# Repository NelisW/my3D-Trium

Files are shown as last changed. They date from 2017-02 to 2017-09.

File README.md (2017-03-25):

# Note

This repository is no longer actively maintained.

The contents of this repository is not an endorsement of the Trium printer. I keep it alive on request of some Trium owners.  

I stopped working on the Trium and I am considering buying another printer.

My own experiences with the Trium is rather negative. 
- If you want to buy a good delta frame to serve as a basis for your own delta printer, it is probably a reasonable design (although I am convinced you can get a less expensive delta frame).
- If you want to learn how to refurbish and rebuild delta printers, this is also a fair kit to buy.
- If you want a printer to print parts and not spend countless hours to get the printer going, rather go buy a well tested design with a large user base. The [Josef Prusa Original i3 MK2](http://shop.prusa3d.com/en/) (not some cheap rip-off) does not cost significantly more than the Trium is has a good reputation (but do your own research).

# Purpose

This repo serves to capture the experience of a number of Trium 3D printer builders.

This repo document is not official Trium information and does not endorse the product in any way. You will find that most Trium users are loyal to the product, but do your own research before committing to a purchase.

The reference information for Trium construction is the [E-Mergin Innovation](https://emergin.net/) Trium printer's  [User Manual (Ver 0.15)](https://emergin.net//user-manual/)  and the assortment of  [videos  on YouTube](https://www.youtube.com/watch?v=81HdwWcrpt0&list=PLMmAHPJoXlL8cp_-7R_6Hdb887jVPCUp3).

This repo contains information that is supplementary to the E-Mergin reference documentation and serves to capture some of the information
-  found on the [Trium ProBoard web site](http://trium3d.proboards.com),
-  found on the [Trium Facebook page](https://www.facebook.com/groups/emergin/) (For my own part, I find the Facebook interface confusing and I don't spend much time there), 
-  learned by a few builders when contructing their Trium printers, and 
-  found on the internet,

# Contents

- [Building the Trium printer](https://github.com/NelisW/my3D-Trium/blob/master/building/Trium-build.md)
- [Calibrating the Trium printer](https://github.com/NelisW/my3D-Trium/blob/master/building/Trium-calibration.md)
- [My views on the Trium printer](https://github.com/NelisW/my3D-Trium/blob/master/building/Trium-gripes.md)

# License

The information presented in this repo is distributed under the MIT license, please see the LICENSE file in this repo.

In particular, please note that 

THE SOFTWARE IS PROVIDED "AS IS", WITHOUT WARRANTY OF ANY KIND, EXPRESS OR
IMPLIED, INCLUDING BUT NOT LIMITED TO THE WARRANTIES OF MERCHANTABILITY,
FITNESS FOR A PARTICULAR PURPOSE AND NONINFRINGEMENT. IN NO EVENT SHALL THE
AUTHORS OR COPYRIGHT HOLDERS BE LIABLE FOR ANY CLAIM, DAMAGES OR OTHER
LIABILITY, WHETHER IN AN ACTION OF CONTRACT, TORT OR OTHERWISE, ARISING FROM,
OUT OF OR IN CONNECTION WITH THE SOFTWARE OR THE USE OR OTHER DEALINGS IN THE
SOFTWARE.

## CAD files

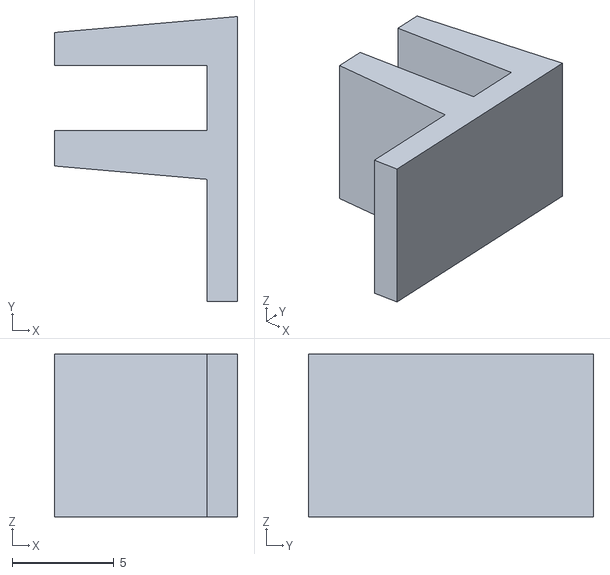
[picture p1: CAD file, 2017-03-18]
parts/TriumSliderHat.stl
9.00 x 14.0 x 8.00

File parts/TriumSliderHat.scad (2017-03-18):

// small part that fits over the slider top to provide
// a better seating area for the end-stop switch

length = 8; // total length
basewidth = 8.;
baseheight = 9.;
overhang = 6.;
overdepth = 1.5;
slotwidth = 3.2;
slotdepth = 8;

rotate([0,-90,0]){
difference(){
union(){
    difference(){
        translate([0,-basewidth/2.,0])
            cube([length,basewidth,baseheight]);
        translate([0,-slotwidth/2.,1.5])
            cube([length,slotwidth,slotdepth]);
    }
 
    translate([0,-overhang-basewidth/2.,0])
        cube([length,basewidth+overhang,overdepth]);
 }
        translate([0,basewidth/2.,0])
            rotate([5,0,0])
                cube([length,2,10]);
   translate([0,-basewidth/2,overdepth])
        rotate([-5,0,0])
            translate([0,-2,0])
                cube([length,2,10]);

}
}

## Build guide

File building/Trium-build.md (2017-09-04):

# Building the Trium Printer

The reference information for Trium construction is the E-Mergin Innovation [User Manual (Ver 0.15)](https://emergin.net//user-manual/)  and the assortment of  [videos  on YouTube](https://www.youtube.com/watch?v=81HdwWcrpt0&list=PLMmAHPJoXlL8cp_-7R_6Hdb887jVPCUp3).

This document is supplementary to the E-Mergin reference documentation and serves to capture some of the information
-  found on the [Trium ProBoard web site](http://trium3d.proboards.com),
-  found on the [Trium Facebook page](https://www.facebook.com/groups/emergin/) (For my own part, I find the Facebook interface confusing and I don't spend much time there), 
-  learned by a few builders when constructing their Trium printers, and 
-  found on the internet,

Several Trium users also freely share their findings and proposals for improvement. MiR did a good job of documenting the build process [here](http://trium3d.proboards.com/thread/67/notes-building-trium-standard-diamond).  This document borrows text and pictures freely from MiR's write up. Several others also contribute freely to the forum and the facebook page and also made comments to this document, these users include janlu, Rajaa Kahel, mikeeitel, Bill B, digid, and others.

References to page numbers in the Trium User Manual (Rev 0.15) are given as pNN.

I am not yet finished building my Trium, neither am I in too much of a hurry to do this quickly. The document will be updated every day or two with the latest information as I proceed. Visit here often to make sure you get the latest version.

This is my first printer and, despite my prior reading, the opened box posed quite a daunting picture. I enjoy writing and sharing  ([here](http://spie.org/Publications/Book/2021423) and [here](https://github.com/NelisW/ComputationalRadiometry)), so I decided to write up my experiences and learning  building up the printer. This document is offered in an effort to help others - especially novice 3d printer builders. My own status as a novice means that I can address some of your questions. I do not provide any guarantee, nor do I assume any liability for the content herein.  If it helps you I am happy, some other day perhaps you can help someone else. This is what open source is all about.

This write-up is somewhat overwhelming in detail and volume. Some proposals here are in the 'nice-to-have' category, e.g., EMI filter, optocoupler bed level sensor interface, etc. Read through the doc, review these proposals and  implement what makes sense to you.  Building the printer should be based on common sense and your intuition. It is however important to read a lot and read widely to ensure that you make an informed decision.  

**Note:** Most of the work we do on the Top Plate electronics and extruder is in the upside-down orientation, which means that left and right are switched.  I frequently found myself forgetting this - always think about the Top Plate assembly orientation when considering left/right or the tower naming convention.

**Note:** Test and review at every step along the build process. You want to catch issues early and not at the end, forcing you to disassemble the printer.  If something is not clear,  search for information: Google is your friend!

**Note:** Get to know the sounds your printer makes. Listen carefully and try to understand what you are hearing.  These noises are the printer's way of speaking to you: learn the langauge.

http://reprapandme.blogspot.co.za/2013/12/the-basics.html

# Tools and consumables

During the course of the build process you would purchase some parts or materials to complete some actions. Most of these are listed below in context of the building process. I recommend that you also consider purchasing the following in some cases you only need a pinch or small scrap! Most of these I would never use in the printer itself, but if you need an M2x25 in the middle of the night, you will be glad having these around.

- A set of machine screws, nuts and washers.  I bough 10 each of M2x6, M2x10, M2x16, M2x20, M2x25, M3x6, M3x10, M3x16, M3x20, M3x25,  M4x6, M4x10, M4x16, M4x20, M4x25, M5x6, M4x10. With as many nuts and washers. 
- A 2 cm strip of thin double sided  tape (not the kind you mount mirrors with).
- A 10 cm strip of magic sticky tape.
- A roll or two of non-adhesive teflon plumbing tape.
- Heat conducting paste (check the operating temperature range, you need at least 260 deg C).
- Cable ties (small) to bind cables into bundles.
- Heat shrink in a variety of sizes.
- Thin machine oil for the ball joints - use sparingly!
- Optional: a six way screw-down terminal block
- Optional: latex or nitrile (medical) gloves  when you work with sticky or lubrication products.
- Optional: in case you need this, some 14 SWG (or 2.5mm2) wire and 22 SWG hookup wire in black and red.
- Optional: some self-adhesive Kapton tape.
- Optional: Loctite thread lock or equivalent - but be careful, once stuck it is hard to remove a screw.

The following tools will come in handy:

- Essential: A set of Allen keys.
- Essential: A set of spanners or wrenches, down to 5 mm. A 7 mm spanner is required to fit the nozzle.
- Essential: A set of jeweller's screw drivers with Allen, Philips and flat heads.
- Essential: Two long nose pliers (short and long).
- Essential: Side cutter.
- Essential: Pencil-style craft knife.
- Essential: Set of flat and Philips screwdrivers.
- Small regular pliers.
- Tweezers.
- A magnifying glass, and/or a ([low magnification](https://www.amazon.co.uk/d/Magnifying-Glasses/Carson-LumiLoupe-Power-Stand-Magnifier/B000CAHCQS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)) 10X [loupe](https://en.wikipedia.org/wiki/Loupe)(jeweller's eyepiece)   to inspect the PCBs and other parts - and your subsequent print quality.
- A toothbrush to brush loosened away debris when cleaning solder bridges from  PCBs.
- Hand drill and drill bits - only used a few times.
- Optional but highly recommended!: a multimeter that can measure AC volts, DC volts, resistance, and possible temperature with a thermocouple.
- Optional: Cutting board or other work surface (don't work on your Oak or Rhodesian Teak dining table).
- Optional but really useful: Heat gun for shrink sleeving. Also used later to heat up the print bed or prints.
- Optional but really useful: Digital or manual vernier caliper. Also used later when calibrating the printer.
- Optional: a k-type thermocouple thermometer that can operate up to 300 deg C. Required to build trust in/calibrate the thermistor.
- Optional: Dremel, but this is just really to play with. I used it once in the TRIUM construction.
- Optional: a set of feeler gauges to use instead of the sheet of paper when setting up the nozzle-bed distance.

You may also find it necessary to have some parts printed using a printing service, simply because your own printer is not working yet.

# Conventions

## Towers
E-Mergin refers to the three vertical parts as "beams".  Beams, in construction, refer to a part that experiences lateral forces. Such parts are normally horizontal and carry downward forces such as weight.  In this document I prefer to use the word "tower" or "column", which signifies a vertical structure.

Label cables for future reference.

There could be confusion with delta printers because the towers are designated by X, Y, and Z, and the cartesian printer coordinates are also designated by the same three letters.  For the purposes of this document the towers are defined in capital letters X,Y, and Z, whereas the coordinate system axes are designated by lower case letters x, y, and z.

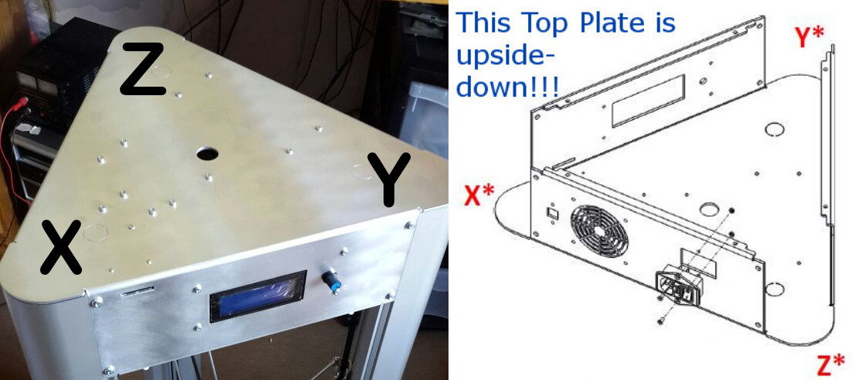
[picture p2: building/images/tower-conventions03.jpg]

[Looking at the front of the printer](https://groups.google.com/forum/#!msg/deltabot/nGpbRPdhAz0/kueyazbXeXAJ) with the LCD facing you (p16):
- X tower is on the front left, Y tower is on the front right, and Z tower is in the middle back.
- The origin (x,y)=(0,0) is in the center between the towers.  This is different from a Cartesian printer where the origin is in some corner.
- Increasing x is left to right, movement to the left of center is -x, and movement to the right is +x
- Increasing y is front to back (toward Z tower). Movement towards the front is -y, movement toward the back is +y.
- z movement is up and down. Touching the print surface is z=0, z_zero or z_min.
- All axis home in the MAX direction
- In the firmware `configuration.h` file the x,y Min/Max values are defined as
		#define DELTA_PRINTABLE_RADIUS 110.0
		#define X_MAX_POS DELTA_PRINTABLE_RADIUS
		#define X_MIN_POS -(DELTA_PRINTABLE_RADIUS)
		#define Y_MAX_POS DELTA_PRINTABLE_RADIUS
		#define Y_MIN_POS -(DELTA_PRINTABLE_RADIUS)
- issue G1 X-50 Y0, Z0: then X will move up, Y will move down and Z will not move. You can also manually move the end effector with the power off and verify it.

## (x,y,z) coordinate system
The following picture obtained [here](https://print3d.com.pk/wp-content/uploads/2015/09/Delta-Kossi-Build-Manual.pdf) shows the coordinate system (not the tower naming) convention in graphical form:
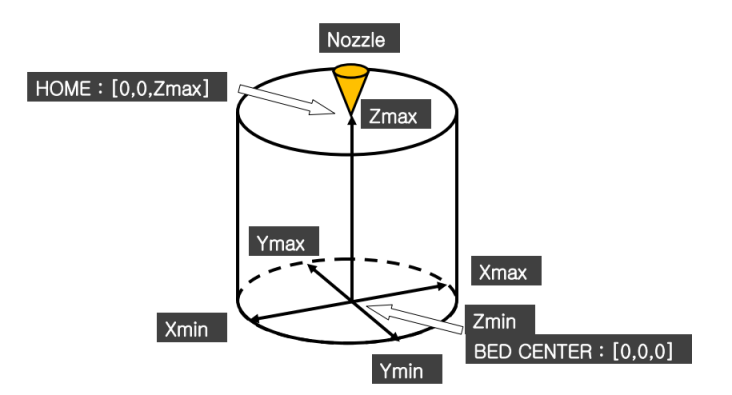
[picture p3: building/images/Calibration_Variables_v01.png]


## Reuleaux print area

A delta printer's print area is defined by the reach of all three delta arms and the actual print area is a clipped [Reuleaux triangle](https://en.wikipedia.org/wiki/Reuleaux_triangle) according to [Ryan Carlyle](https://groups.google.com/forum/#!topic/deltabot/xH_FIgClU9k).    The actual Trium print area will be the intersection of the hot bed circle and the Trium's Reuleaux triangle.

# Notes

## Software

This document does not cover software issues.  Before using the printer be careful to [set up the software](https://www.youtube.com/watch?v=bPBlYPV2sME&index=19&list=PLMmAHPJoXlL8cp_-7R_6Hdb887jVPCUp3) to the correct settings. In particular, the slicers must be set up for the Trium delta printer defaults.  The slicer software does *not* work correctly by default straight from the box.

## Noise damping

The all-metal Trium frame is superbly stiff and stable.  However the stiffness means that it resonates well (and at high frequency) and hence propagates vibration noise very, very well. This increases the overall noise level: anything that moves anywhere causes some resonance noise somewhere else.  For this reason apply vibration damping where ever you can. A case in point: slide a metal object across the Top Plate air vents; they ring very nicely at a high frequency. Fixing some rubber or silicon to the inside of the vent strips should reduce this particular vibration mode.  Fortunately, because of the superb frame stiffness the resonance frequencies are quite high - which means small displacements with lower energy; which should be easier to dampen.
- There is  a [design for a set of damping foot pads](https://www.facebook.com/groups/emergin/permalink/1870842983153461/) on [thingiverse](http://www.thingiverse.com/thing:2041200).
- You can use noise dampers on the tower stepper motors (see below).
- Rajaa replaced the rod-retaining springs with a rubber band to reduce spring noise.
- Replacing the DRV8825 drivers with [TMC2100 drivers]( https://www.facebook.com/groups/emergin/permalink/1869317553306004/) (not yet fully sorted out).
- Add an inline switch to the print cooling fans so that they can be switched off when not used. Do *not* switch off the fans on the electronics or print head heat sink.
- Jean Marc Cierniewski investigated using [small o-rings when mounting fan ducts](https://www.facebook.com/groups/emergin/permalink/1871767846394308/), but believes that there is more vibration on the rods.  However, using these o-rings on the main cooling fan mounted to the aluminium frame made a big difference.  You could also use rubber grommets to mount the fan.
- I pushed in a narrow strip of high density packing foam between the power supply and the Top Plate air vents to dampen the vibration of the vent strips.  There is a little vibration, but it diminishes quickly.
- I also put compacted  plastic foam sheeting inside each tower to dampen the ringing.

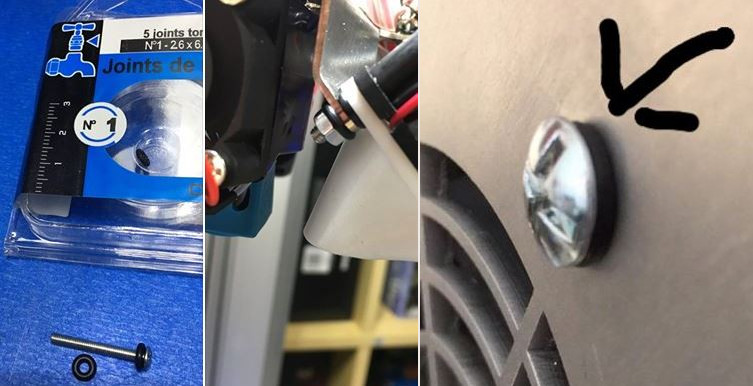
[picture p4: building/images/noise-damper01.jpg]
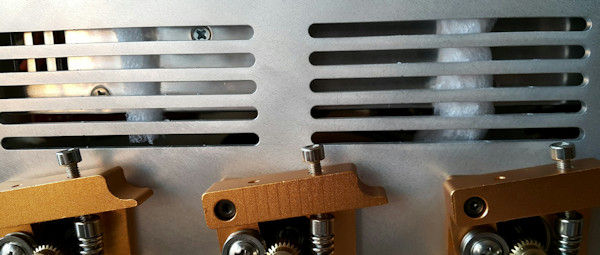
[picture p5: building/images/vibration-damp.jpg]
 

## Electrical supply safety

If wired correctly, the electricity supply convention in most parts of the world (except the US, it seems) is as follows:

- The green (or green/yellow) wire is 'ground'/'earth',  linked to a low resistance peg driven into the soil at your house, fixed to a conducting water pipe or linked to a peg driven into the soil at your electricity utility connection point (in the street or at a local substation).  This is the best reference of zero voltage under normal conditions.   If your feet are touching wet soil and you touch the earth/ground wire nothing will happen.
- The blue wire is 'neutral' (also known as null) meaning that it should normally be at a low voltage relative to earth. Depending on the local electricity safety code, neutral is normally connected to earth/ground at the point where the electricity enters your house. If your feet are touching wet soil and you touch the neutral wire nothing will happen under normal circumstances.
- The brown wire is 'live' and is at 115 or 230 V relative to neutral. This is the dangerous wire. Under normal circumstances the electricity flows between live and neutral. No current from live/brown ever flows to the green/earth wire (if it does, this is called a fault condition). If your feet are touching wet soil and you touch the live (brown) wire the electricity will flow from live, through your body and feet into the earth/ground, potentially killing you in a most unpleasant manner.
- Most electricity safety codes require a device (residual current device or earth leakage relay) which measures the difference in current flow between live and neutral. If this current exceeds some small value (20 mA) it means that some current from live is flowing to earth: an undesired fault condition.  The device then breaks the electricity supply - not because of over-current but because of current earth leakage.

All of the above apply when a three-pin connection is made to the electricity supply. If your country only have a two-pin supply or if your cable only has two pins and no earth conductor, the situation is very different. The wall plug can be plugged in in any orientation: there is no distinction between Live and Neutral any more. And even worse, there is no Earth connection.  Also, despite electricity safety codes' requirements, it may be that in some cases the Live and Neutral wires are exchanged, so that the terminal labelled with 'Neutral' may in fact be live.  This can happen is someone wired a plug the wrong way around - which happens frequently.  

According to [this video](https://www.youtube.com/watch?v=Bqar4cuVF_A), the colour code (or is it color code?) in the US is as follows. So please translate the colours to your local custom.  Please take the time and watch this video.

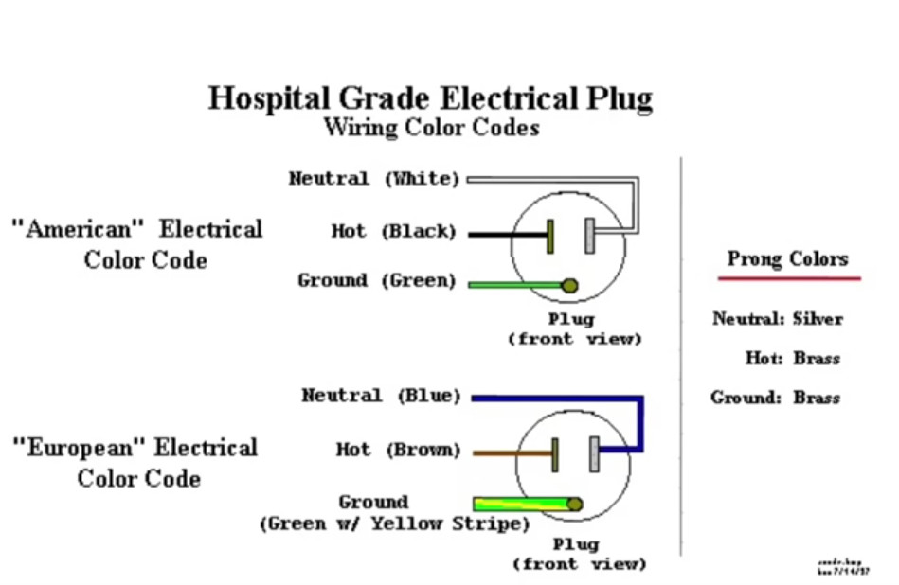
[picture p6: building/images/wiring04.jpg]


**So please consider the Neutral/Null and Live wiring in your printer as equally dangerous. Always afford Neutral the same respect you would show Live!**

**Never connect Neutral/Null or Live to Earth in the printer, it may lead to earth leakage conditions.**  Connecting Earth to Neutral is your electricity supply utility company's concern, they will do it according to their codes. Don't violate their codes by doing it yourself in your house or in your printer.

**Never connect Neutral/Null or Live to your Trium case,  or if your supply only has two wires, don't connect either to the case.**

### Connecting the Trium frame/case
At this point the issue of case earthing or grounding should be considered. The question is which of these do you connect and why?  There are three 'zero' potential locations to consider:

- Your 115/230V earth/ground, the green (green/yellow) wire from the house network (if Earth is available).
-  The Trium metal case.
-  The power supply zero voltage terminal (by convention zero voltage is normally the negative (black or -) terminal in the bipolar power supply, whereas the positive (red or +) is at some non-zero voltage (12V in this case).

The User Manual does not prescribe any connection: all three a disconnected from each other (if there are no connections inside the power supply, which is normally the case).  All three therefore 'float' with respect to each other: there can be some voltage between any of these.

If you are at all unsure, follow the Trium instruction, but just be very careful with the mains wiring!

For more information see [here](http://www.ese.upenn.edu/detkin/instruments/misctutorials/Ground/grd.html), [here](https://celectronics.com/pdf/IEEE11-9-05.pdf), and [here](http://www.allaboutcircuits.com/textbook/direct-current/chpt-3/safe-circuit-design/). See also [this video](https://www.youtube.com/watch?v=Bqar4cuVF_A)

#### Earth connection
If you have a three-pin electricity supply: 
Let us review connecting the electricity supply Earth to the Trium case with a secure and low resistance bond.  In this case the earth leakage protection will work if you accidentally touch the case and live.  The procedure is normally followed in domestic devices containing metal frames (bed lamps, clothing irons, stoves, kettles, etc.).  From a human safety and fire hazard perspective this is the safest approach.  You make your own decision.

If you have a two-pin electricity supply, there is no Earth to connect to the case. **Don't connect either of the two wires to the case**.

#### Power supply connection

It the printer electronics PSU module zero (black wire) is not connected to the frame, it means that the electronics reference floats with respect to the frame.  Any part of the electronics can touch the frame with no ill effect.  The disadvantage of this approach is the EMI is harder to control because the frame/case is floating with respect to the electronics.

If the power supply 0V negative/black is securely connected to the chassis, the case is not floating with respect of the electronics and EMI is easier to contain. However, because the frame is now at the 0V reference, if the +12V or some electronics output now touch the frame it will result in a short circuit fault, possibly destroying electronics components. For this reason some people prefer to fit a low resistance 100-1000 Ohm between the case and negative/black which will somewhat limit the current flow under fault conditions, but prevent electrostatic voltage build-up damage to the electronics.

#### Where to connect to the frame/case

Generally speaking, bonding the Earth (if done) and the printer power module to the case should be done at one point and one point only. Do not rely on the case to provide ground current flow (this will lead to earth loops and the EMi will be worse). So the electronics ground wiring should never touch the frame, except at this one point. In some cases it may have benefits to have the frame as ground plane, but it requires very careful design and is outside the scope of this project.

My preference would be to take two wires (one from green/earth and one from negative black) and connect both to a single point on the chassis.  You decide for yourself.

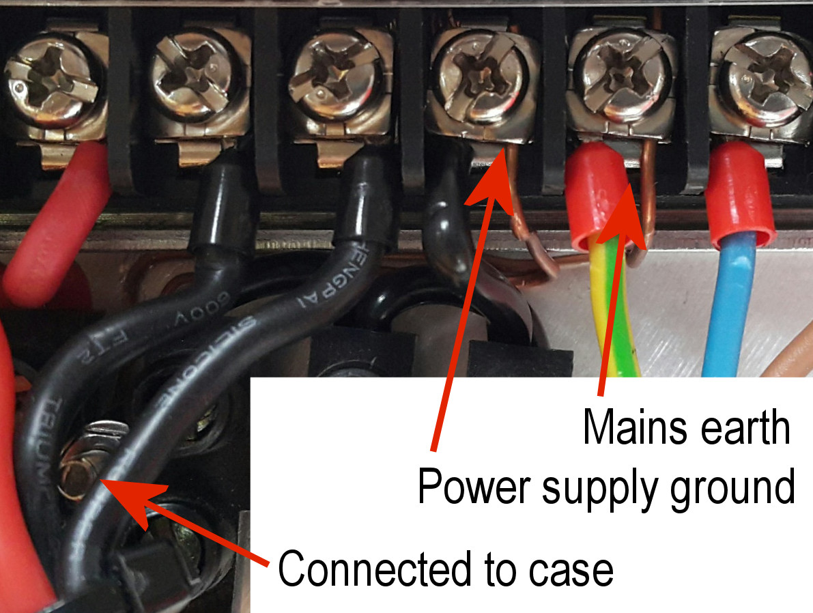
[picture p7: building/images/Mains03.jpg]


### Supply wiring safety test

**Please do this test!**  
*In the entire procedure below the printer should not be plugged into the electricity supply in the wall.*  We want to measure the wires that normally carry lethal voltages when plugged into the wall. So please pull the plug and keep it pulled.  In this procedure we assume that your house wiring is done correctly and we now want to verify that the printer and cable used with the printer is set up correctly.
- Unplug the black printer supply cable from your mains connector in the wall.  In other words, pull the mains plug well free from the electricity supply.  And keep it free for the entire test.
- Plug the kettle cord side into the C14 connector on your printer (the C14 is the thing in the pictures below).
- Switch off the C14 switch on the printer (0 position).
- Use the table below and measure the continuity between the pins on the plug that normally goes into the wall (but don't plug it into the wall!!!) and the wires on terminal on the printer's power supply (picture above).

|- | Earth (green/yellow)| Neutral (blue)| Live (brown)|Frame|
|----|:----:|:----:| :----:|:----:|
|Earth pin on plug| *conduct* |**open**| **open**|your choice|
|Neutral  pin on plug|**open**|*conduct*|**open**|**open**|
| Live  pin on plug|**open**| **open**|*conduct* if C14 'on'|**open**|
| Live  pin on plug|**open**| **open**|*open* if C14 'off'|**open**|

- Depending on whether the C14 switch is on or off the live should conduct or open.
- Measure the full matrix of possibilities above and make sure that your results exactly match the table above.  If you have a *conduct* on any position where it should be **open** please take your printer to a certified electrician to correct. This really important and you could kill yourself or a member of your family if you are reckless in this regard.
- Now remove all measurement equipment from the printer, ensure that there are no wires touching the Neutral or Live wiring in the printer.
- Tip: never make temporary connections to Live or Neutral with the intent to remove it later.  The devil will have it that such wires stay and you may hurt yourself, despite your best intentions.

## The light in the power switch

The power switch has a light to indicate the power status.  The Trium Manual does not show how to wire the switch for activating the light when power is on.  [Justin Smith shows](http://www.doityourself.com/forum/electrical-ac-dc/529348-need-help-wiring-inlet-male-power-rocker-switch-lighted.html) how to connect the light. However, his description was the wrong way around for my switch!  After some sparks and one power over-current trip I came to the conclusion that there are two possible wiring options, depending on the orientation of the switch (see below).

Only deviate from the Trium-proposed wiring if you really know what you are doing (or get a certified electrician to do this for you).

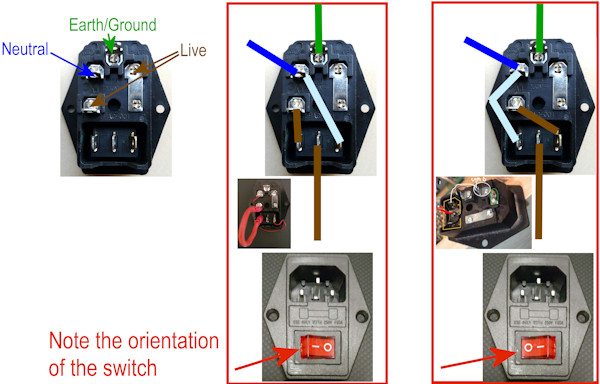
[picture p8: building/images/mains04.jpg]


## Printer PSU Operating voltage

The Trium printer uses a 12 V power supply.  Under certain circumstances you may want to increase the power supply voltage up to 14 V.  The Arduino board has a voltage regulator and can take higher voltages.  None of the components on the RAMPS board could destruct at 14 V, so it seems nominally safe to operate at up to 14 volts.

Why would you want to do this?  The heaters in the hot end and hot print bed have fixed resistance values. By increasing the supply voltage they can reach higher temperatures. Increasing the supply from 12V to 14V will increase the power dissipation by 36%, which is substantial.  

Keep in mind, however that many components (LED lamps, fans, etc) are rated for 12 V operation, so you would need to lower the voltage on these by a secondary regulator or by dropping the positive supply voltage with three diodes in series (3x0.6V=1.8V).

Generally speaking you lower electronic/electric component failure rates by working at the lowest current or voltage where the device still works correctly.

## Electric mains spikes, filters and USB

Spikes on the mains supply can cause problems with electronic equipment, see [here](http://7ms.com/enr/online/2010/02/notebook.shtml) and [here](http://www.emcfastpass.com/avoid-the-most-common-failures-with-these-7-essential-emc-design-rules/). Something switched on in the house somewhere causes some effect in the printer. Apparently this effect is worse [when using USB](https://m.facebook.com/groups/1798144480423312?view=permalink&id=1863328043904955), see also [here](http://www.st.com/content/ccc/resource/technical/document/datasheet/ae/09/87/c5/c7/6b/4e/8a/CD00002023.pdf/files/CD00002023.pdf/jcr:content/translations/en.CD0000202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).  The failure appears randomly in the print, not always one the same layer.  Obviously, the longer the print time, the bigger the risk that the print might be interrupted.  Try so see if a better quality USB cable can prevent the problem.

If the spikes arrive via the mains power supply, the best solution is to install a EMI filter or spike protection device in the mains power supply.  This EMI filter is not the same as a surge arrestor.  The surge arrestor prevent over-voltage conditions (i.e., lightning) by short circuiting itself.  The EMI filter has no effect on the supply voltage, but suppresses spikes or other high frequency noise on the supply wires.  The use a and design of these filters are given [here](http://www.eetimes.com/document.asp?doc_id=1230404) and [here] (http://www.emfrelief.com/capacitive-filters.html).  These filters are not often built into mains extension leads or distribution panels.  The filters can be bought in [PCB format](http://www.ebay.co.uk/itm/3900W-EMI-18A-High-Frequency-Power-Filter-Board-DIY-Kits-For-Speaker-Amplifier/262372720254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) or packaged in a [small case](http://www.ebay.co.uk/itm/TDK-Lambda-250V-10A-EMC-EMI-Line-Noise-Filter-IEC-Socket-/172143349786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) or even a [C14 switch](http://www.ebay.co.uk/itm/CW1D-10A-T-IEC-320-C14-EMI-filter-AC115V-250V-w-Boat-Switch-w-Fuse-Holder-/121724133961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).  When you buy such a filter, just make sure that it can operate at the power ratings used in 3D printers.

## Auto shut off

Given the heat a 3D printer can generate, even when idle, Jeremie Francois would better [auto switch it off](http://www.tridimake.com/2012/11/auto-shutoff-at-end-of-print.html)  than let it powered unattended. In the case of Trium printers, I would also like to switch off when the magnetic bearings disengage.  Francois  used a relay to control the mains power supply. He controls the relay with the `A0` pin on the Arduino. The printer is started with a push button which powers on the printer, making `A0` go high.  The `A0` pin fires up the relay and power is sustained through the relay (`A0` remains high).  To auto switch off, add the `M81` command as the last command in the gcode. This command makes the pin `A0` go low and the relay releases, dropping power to the printer.

## Trium modifications to the Marlin firmware

See the separate file [Trium-firmware.md](https://raw.githubusercontent.com/NelisW/my3D-Trium/master/building/Trium-firmware.md)

# Components used in the Trium

## Stepper motor

Trium uses the [MT-1703HS168A 43Ncm](http://www.motechmotor.com/products_detail.php?id=147&cid=&page=1) [stepper motor](http://forum.arduino.cc/index.php?topic=284828.0) with the following specification:

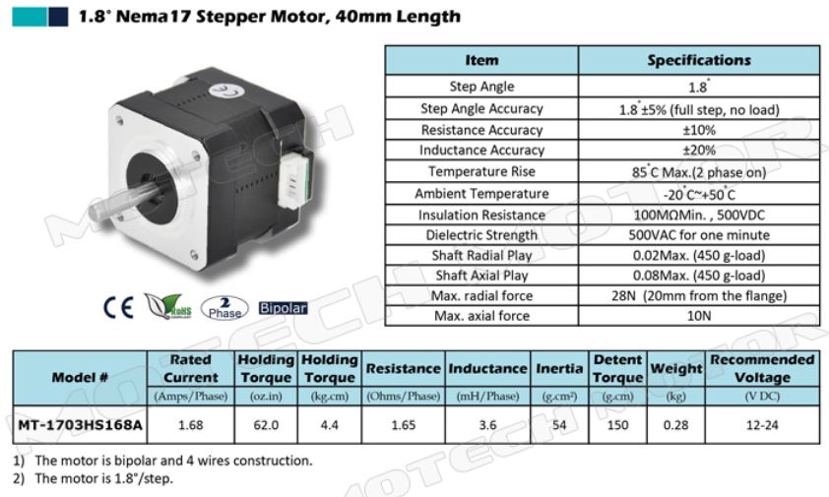
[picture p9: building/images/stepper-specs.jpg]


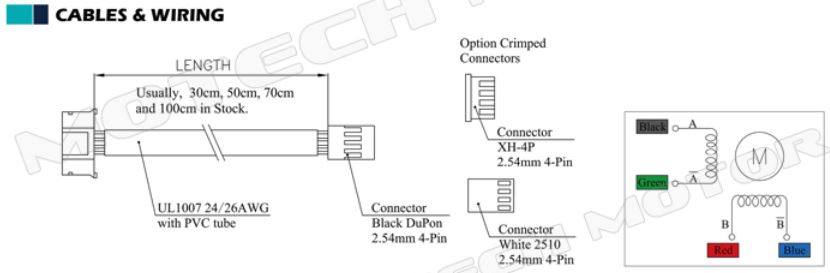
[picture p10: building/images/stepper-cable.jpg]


The Trium stepper motor has a maximum current rating of 1.7 A with a 1.67 Ohm coil resistance, which indicates a maximum motor supply of 2.8 V (using Ohm's law).  Using this motor with 12 V would allow higher step rates, but the current must actively be limited to 1.7 A to prevent damage to the motor.

## DRV 8825

The DRV8825 driver schematic diagram shows the trim potentiometer used to set the current limit. The current is limited to 2xVref. The Polulu diagram below shows a 10 kOhm trimpot, but the average resistance measured on the PCBs supplied with the Trium is around 7.67 kOhm. The Trium instruction is to set the resistance between Vref and GND to 2.2 kOhm.  Simple math shows that Imax = 2xVref=2x3.3x2.2/7.67=1.9A, with Vref=0.95V.  It seems then that the Trium stepper motors are driven somewhat (10%) beyond the design rated current.

The end-to-end resistance of the six DRV 8825 trimpots for my printer measured 7.5, 7.4, 8.22, 7.61, 7.73, 7.59 kOhm.  This means that the current limits range from 1.77 A to 1.9 A. This 6% spread is probably fine, but if you require more accurate settings, it would be better to adjust the trimpots to a fixed voltage, rather than to fixed resistance between ground and common.  In my first build I set the reference voltage to 1.7/2=0.85V, which is the 'design point' for the stepper motor.  During printing, the printer appeared to loose steps during repeated checks on z calibration (see the later discussion, towards the end of the document). This could be because of too low current or too high friction. I decided to increase the calibration voltage to 0.96V for the three tower stepper motors, which implies a current of 1.9A (10% above rated current).  The extruder calibration voltage was kept at 0.85V.

See the notes below in the extruder section where it is described why and how the extruder motor current limit setting should be adjusted to prevent filament grinding.

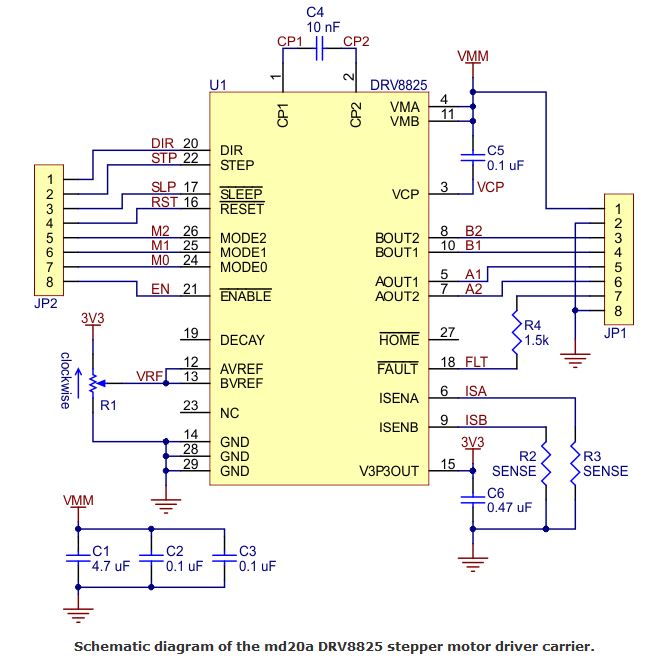
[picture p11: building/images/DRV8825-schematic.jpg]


The boards supplied with Trium are not Polulu driver boards, but some useful information are given [here](http://reprap.org/wiki/Pololu_stepper_driver_board), [here](https://www.pololu.com/product/2132), and [here](https://www.pololu.com/product/2133), read with the necessary care.

## RAMPS board circuit diagram

The RAMPS circuit diagram is available [here](http://reprap.org/mediawiki/images/3/3f/Arduinomegapololushieldschematic.png) and [here](https://download.lulzbot.com/AO-100/hardware/electronics/RAMPS_1.4/RAMPS_1-4manual.pdf). and [here](http://www.reprap.org/mediawiki/images/0/06/RAMPS_dossier.pdf).

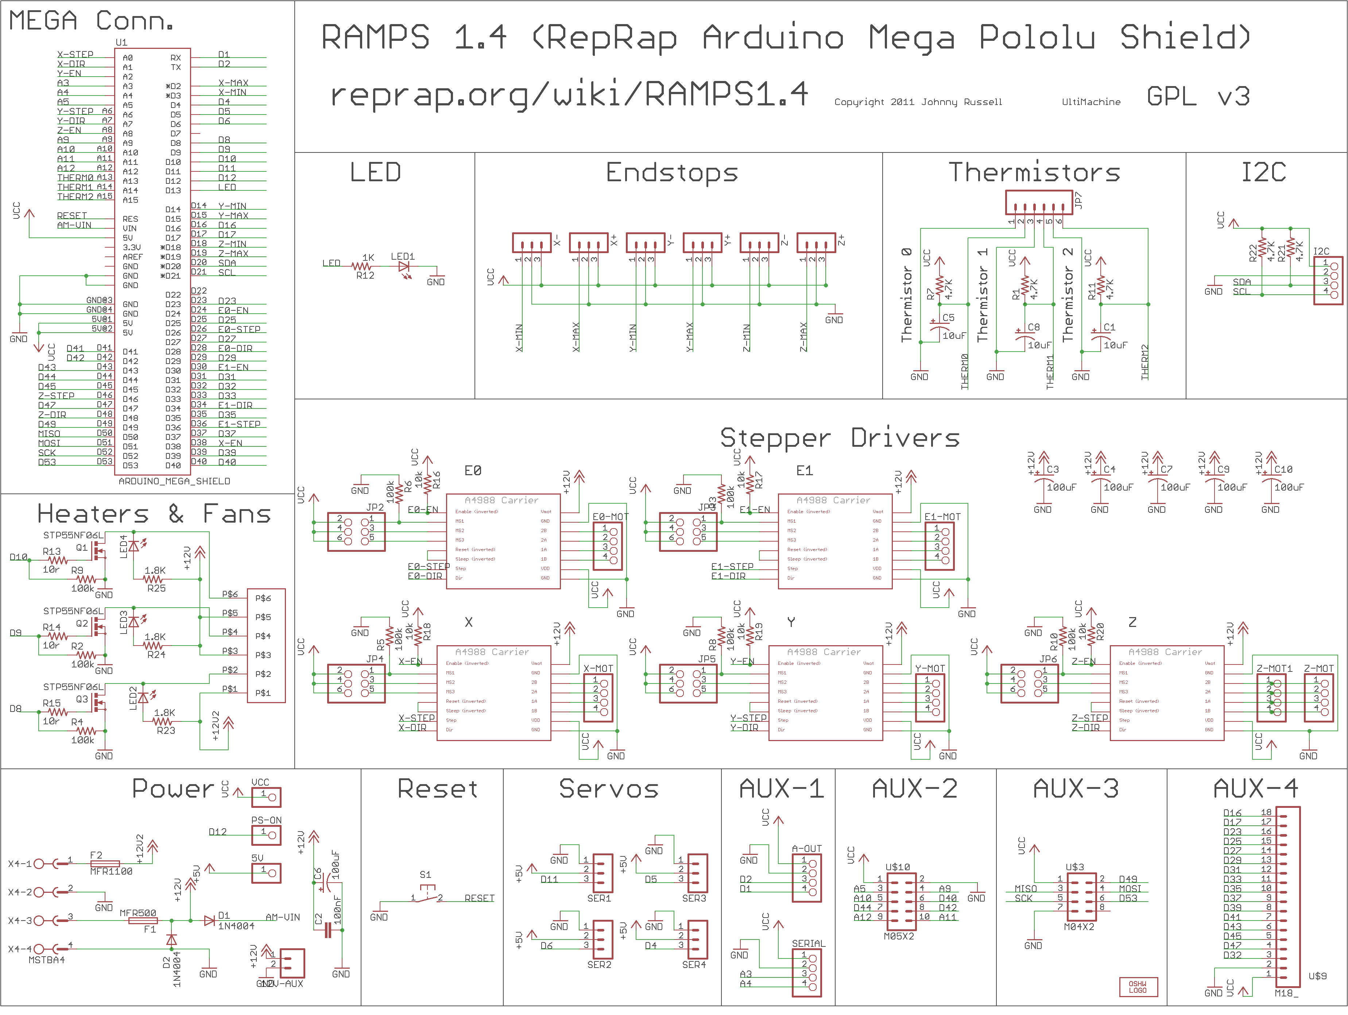
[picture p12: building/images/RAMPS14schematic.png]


Also see the very useful [RAMPS information wiki](http://reprap.org/wiki/RAMPS_1.4), such as component identification, jumper settings and connecting to the RAMPS.  The wiring shown on this page is not fully Trium compatible, so read with care.

## Thermistors

The thermistor used by E3D-Lite6 is not the same as the one uses with E-Mergin hot end and the Diamond hot end.  Both have 100kOhm resistance at 25 deg C, but they have different [B or beta temperature coefficients](https://en.wikipedia.org/wiki/Thermistor). So, just measuring the resistance at room temperature will not help you discriminate between the two sensors: measure with the sensor at a known elevated temperature (see value below at the boiling point of water - don't put the open thermistor in the water, it is not waterproof). To measure the resistance values around room temperature is not sufficient, because the resistance differences are within sensor tolerance.

-  The E3D hot end ([firmware here](https://emergin.net/download/marlin-rc7-trium3d-e3d-26-11-2016/)) uses  the [104GT-2 Semitec](http://www.atcsemitec.co.uk/pdfdocs/GT-2-glass-thermistors.pdf) 100kOhm NTC Thermistor, with beta=4267K, nominal resistance values of

|Temperature | Resistance kOhm |
|----|----|
|20|126.8|
|25|100|
|50|33.49|
|100| 5.56|
|150|1.36|
|200| 0.439 |
|250|0.1475|

-  The standard E-Mergin and Diamond hot ends ([firmware here](https://emergin.net/download/marlin-rc7-trium-22-nov-2016/)) uses (according to the BOM) a [cheap 3950 thermistor](https://cdn.shopify.com/s/files/1/0658/7659/files/NTC-Thermistor_3950_Datenblatt.pdf) with beta=3950K, which has a nominal resistance

|Temperature | Resistance kOhm |
|----|----|
|20|125.25|
|25|100|
|50|35.9|
|100|6.7|
|150|1.77|
|200|0.582 |
|250|0.23|

Investigate the [temperature measurement](http://reprap.org/wiki/Thermistor) resolution. The 3950 thermistor temperature resolution values are investigated here.  From the RAMPS circuit diagram I conclude that there is no resistor in parallel with the thermistor and hence the sensor resolution in the range 230C to 250C is about 1 ACD unit per deg C.

	ADC_count = 1024*Vout/Vref = 1024* Rth /(R2+Rth)  # for 100K thermistors without parallel resistor

|Temperature | 3950 Resistance kOhm | ADC|
|----|---|----|
|230|0.328|66.8|
|250|0.23|47.7|

The two TRIUM firmware versions ([standard/DH]((https://emergin.net/download/marlin-rc7-trium-22-nov-2016/) and [E3D](https://emergin.net/download/marlin-rc7-trium3d-e3d-26-11-2016/)) differ in the file `Configuration.h` file: different temperature sensor `TEMP_SENSOR_0`.
- The E3D uses sensor 5: "100K / 4.7k - ATC Semitec 104GT-2 (Used in ParCan & J-Head)"
- The standard hot end uses sensor 11: "100k / 4.7k beta 3950 1%".

The thermistor resistance values given above are open circuit values, but in the RAMPS board these thermistors are in a [circuit ](http://reprap.org/wiki/Thermistor) voltage divider configuration with a 4.7 kOhm resistor, with a noise filtering capacitor to ground.

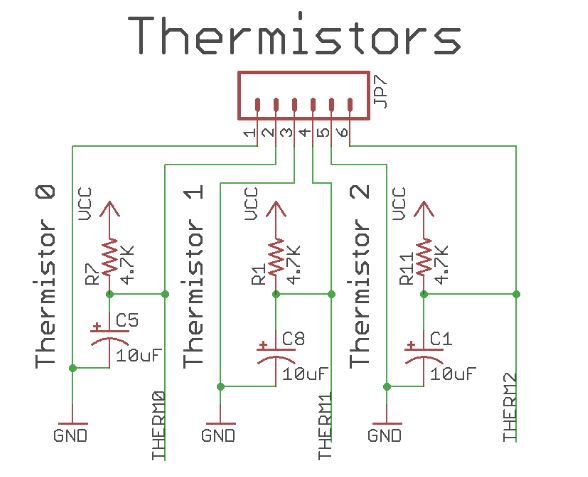
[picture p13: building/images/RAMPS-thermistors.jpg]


It would not normally be necessary to calibrate your thermistors, but if you need to, see [here](http://reprap.org/wiki/Thermistor), [here](http://www.thingiverse.com/thing:103668), [here](https://github.com/reprap/firmware/blob/master/createTemperatureLookup.py), and [here](http://hydraraptor.blogspot.co.za/2007/10/measuring-temperature-easy-way.html).

## Rod and ball replacement

Steffen Bleich had a mishap where some rods broke.  He ordered this rods [here](https://www.ultibots.com/magball-arms-288mm-delrin/) in the hope that it will work also fine or maybe even better.  The rods obtainable [here](https://www.ultibots.com/magball-ends-set-of-12/) already include the required 12 balls and nuts. The balls have a M3-thread and should fit fine into the Trium hardware. The maker of the rods is [this company](https://groups.google.com/forum/#!msg/deltabot/mPw1SJ2f9Vw/55vmV3sPDQAJ).

## Bed levelling sensor

The inductive sensor reacts to metal only (not to glass). The 4 mm detection range apply when used with iron, [for aluminium the distance](https://3dprint.wiki/reprap/anet/a8/improvement/autobedlevelling) is around 1.2-1.5 mm (so don't use a glass bed on top of the aluminium).

The sensor needs a power supply from 6 to 36 V (12 V for the Trium). The output signal can then potentially swing between near zero to the sensor supply voltage - and this could exceed the allowable voltage on the Arduino input pin. In this case some voltage conditioning is required. Sometimes the sensors are working at 5V (the voltage delivered by the RAMPS board), however, most of the sensors need a higher voltage to work.

The Trium BOM states that a LJ12A3-4-Z/AY sensor is used (2017-01-15).   The wiring modification E-Mergin supplied on the [KickStarter page]((https://www.kickstarter.com/projects/873464596/trium-delta-3d-printer/posts/1754830) shows a LJ12A3-4-Z/BY.

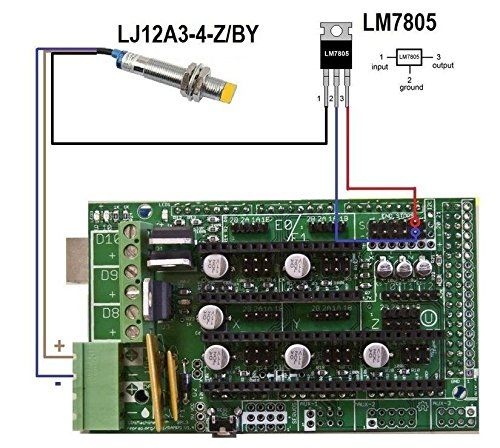
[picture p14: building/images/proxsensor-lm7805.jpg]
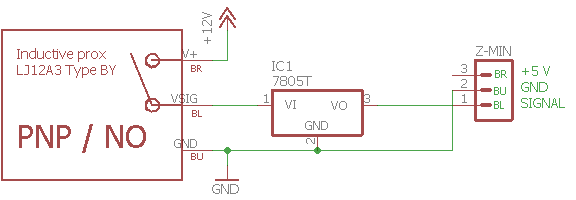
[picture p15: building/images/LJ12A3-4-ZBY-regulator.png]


You can see which sensor was delivered with your kit by looking at the small label on the device.  My kit, as delivered contains one LJ12A3-4-Z/AY sensor and one LJ12A3-4-Z/BX. The LJ12A3-4-Z/BY wiring supplied on the Trium KickStarter page therefore *does not apply to my sensors*.  The Chinese suppliers appear not very diligent on delivery of the exact model you ordered. The electronics circuits and firmware settings for each of these three types are different, so what works for the one will not necessarily work for the other.  I put together information from a number of sources in the tables below to show the differences between the different sensors. In the figure below I show a switch but in the hardware a transistor or FET is used: so it is not just an isolated switch, it has voltage levels referenced to the rest of the electronics.

|[Model](https://opencircuit.nl/ProductInfo/1000064/LJ12A3.pdf) | Config | Switch |Where identified|In my kit|
|----|----|----|----|----|
|LJ12A3-4-Z/AY|PNP|NC|BOM|Yes|
|LJ12A3-4-Z/BY|PNP|NO|Wiring picture|-|
|LJ12A3-4-Z/BX|NPN|NO|-|Yes|

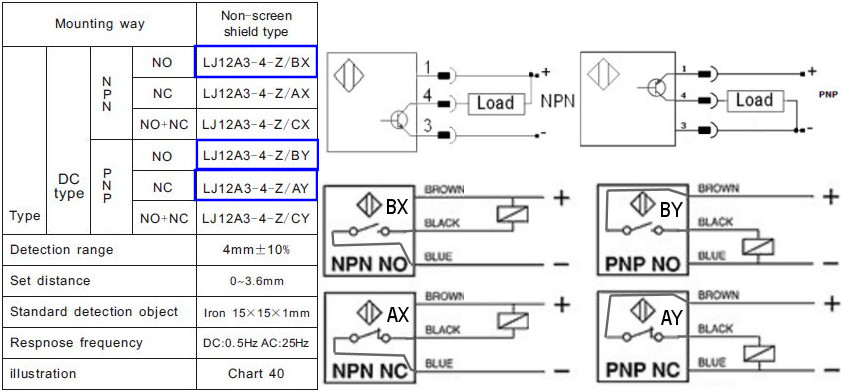
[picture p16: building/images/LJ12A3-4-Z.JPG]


Designing an interface between the sensor and the Arduino is [further complicated](https://3dprint.wiki/reprap/anet/a8/improvement/autobedlevelling) by the fact that the open collector status of the sensor is not known (Chinese versions apparently mostly/often have pull-up resistors internally to the sensor: there could be a voltage on the black wire).  Depending on your sensor:
- NPN with no internal pull-up resistor to +V (open collector): safe to use with 5V Arduino.  Just connect to the board, but switch on the Arduino internal  pull-up resistor or add one externally.
- NPN with an (unknown value) sensor-internal pull-up resistor to +V: the voltage on the sensor  output may exceed 5V when not triggered. Some form of voltage conditioning is required; internet posts propose optocouplers, voltage dividers or diodes in various configurations.
- PNP output voltage will always swing between near zero and the sensor supply voltage. Some form of voltage conditioning is always required; internet posts often propose voltage dividers.

To determine if the sensor is open collector, wire it up and measure the output voltage (black) with respect to ground (blue). When triggered, if the output voltage does not change significantly it is open collector.  If there is an internal pull-up resistor the measured signal voltage will change.

The [MEGA 2560](https://www.arduino.cc/en/Main/arduinoBoardMega2560) digital pins have internal pull-up resistors of 20-50 kOhm that are by default *disconnected* from the pin. A pin can be connected to the internal pull-up resistor by a firmware command (not sure what Marlin does).  Any external resistor network connected to the pin will be affected by the internal pull-up resistor, if connected by firmware. So be careful when devising voltage divider circuits.

Most logic conventions assume a high value to mean a triggered value and a low value to mean the absence of the trigger (this is known as positive logic).  Depending on the normally open (NO) or normally closed (NC) option and the NPN/PNP configuration, the sensor logic can be positive or negative.  Hence,  you must set up the firmware to match the logic of the sensor. The Trium the sensor is connected to the ZMIN endstop pin (ZMAX is connected to the switch).   In Trium we are using ZMIN to serve as the probe (not as a limit switch), so the standard ZMIN flag for the limit switch must be set.  In Marlin the ZMIN logic convention is defined in the line `#define Z_MIN_ENDSTOP_INVERTING xxxx` in the file `configuration.h`.   Set the value to `false`  if you are using positive hardware logic.  The  `Z_MIN_PROBE_ENDSTOP_INVERTING` has no effect, because it is not tested given the rest of the flags in the configuration.h file. So for my positive probe hardware logic the settings must be

	// Mechanical endstop with COM to ground and NC to Signal uses "false" here (most common setup).
	#define X_MIN_ENDSTOP_INVERTING true  // set to true to invert the logic of the endstop.
	#define Y_MIN_ENDSTOP_INVERTING true  // set to true to invert the logic of the endstop.
	#define Z_MIN_ENDSTOP_INVERTING false  // set to true to invert the logic of the endstop.
	#define X_MAX_ENDSTOP_INVERTING true  // set to true to invert the logic of the endstop.
	#define Y_MAX_ENDSTOP_INVERTING true  // set to true to invert the logic of the endstop.
	#define Z_MAX_ENDSTOP_INVERTING true  // set to true to invert the logic of the endstop.
	#define Z_MIN_PROBE_ENDSTOP_INVERTING irrelevant  // set to true to invert the logic of the endstop.

|xxxx |NO|NC|
|----|----|----|
|PNP|false |true |
|NPN|true |false |

So in my case with both NO and NC sensors, it seems that I would have to re-flash the firmware for changing logic  when changing printing heads.  A better solution would be some electronics on the printing head that will always give a consistent polarity output.

After some consideration I decided on the following solution (the Z/AY circuit was built and it works very well). The idea is to employ an optocoupler circuit to take care of the voltage incompatibilities and also to configure the output logic to be positive (1 for proximity and 0 for not proximity), irrespective of the sensor on my print head.  The wiring for each sensor configuration is slightly different but the output logic to the Arduino firmware is consistent between the variants.  The component values are selected for a 10 mA LED current and assuming a 1:1 ratio between LED current and transistor current.  Depending on the value of the Arduino internal pull-up resistor the NO `low` voltage will be between 0.3 and 0.7 V.  The sensor positive supply voltage will be 12 V, taken from the red heat sink cooling fan wire, and the ground will be taken from the black heat sink cooling fan wire. Cut the three sensor wires (BR=brown, BU=blue, BL=black) and insert the optocoupler components as shown below.  

Don't connect the 12V and 5V grounds together, keep them separate at the optocoupler - there is no need to connect. If fact, if you connect them you create an earth loop which is potentially bad for EMI.

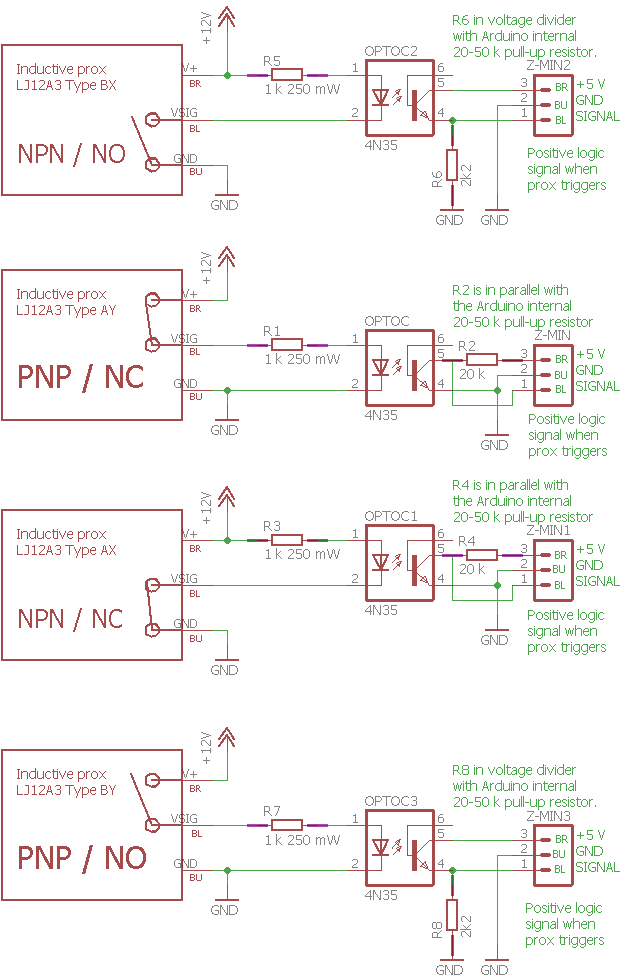
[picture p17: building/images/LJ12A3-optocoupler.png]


Test the probes operation [as follows](https://www.repetier.com/documentation/repetier-firmware/z-probing/): 
First check is always if signals are correct. So send M119 and see that z probe shows a “L” for low = not triggered. Now trigger it by hand while sending M119 again. Now probe value should show a “H” for high = triggered. If it is the other way around you need to change `Z_MIN_ENDSTOP_INVERTING` (`Z_PROBE_ON_HIGH` for Repetier firmware). If nothing changes you have either the wrong pin used or configured, or pull-up must be different. Fix it and continue.

For more information see
[Repetier firmware z-probe details](https://www.repetier.com/documentation/repetier-firmware/z-probing/), 
[description of how the sensors work](http://www.ab.com/en/epub/catalogs/12772/6543185/12041221/12041227/print.html), [description and circuit diagram](http://www.electroschematics.com/12295/inductive-proximity-switch-w-sensor/), [optocoupler connection](http://electronics.stackexchange.com/questions/101624/how-to-connect-a-inductive-proximity-sensor-switch-npn-dc6-36v-to-pic18f4550-5v), [here](http://forums.reprap.org/read.php?219,533688,539308), [here](http://electronics.stackexchange.com/questions/101624/how-to-connect-a-inductive-proximity-sensor-switch-npn-dc6-36v-to-pic18f4550-5v), [here](http://www.thingiverse.com/thing:539692), [here](http://forums.reprap.org/read.php?219,533688,539308), [here](http://www.printrbottalk.com/forum/viewtopic.php?f=21&t=7372), [here](https://3dprint.wiki/reprap/anet/a8/improvement/autobedlevelling), [here](http://www.fabric8r.com/forums/archive/index.php/t-1745.html), [here](https://www.theautomationstore.com/npn-pnp-devices-and-connections/), [here](http://www.instructables.com/id/Enable-Auto-Levelling-for-your-3D-Printer-Marlin-Fi/?ALLSTEPS), and [here](https://sensortech.wordpress.com/2011/01/18/industrial-sensing-fundamentals-%E2%80%93-back-to-the-basics-npn-vs-pnp/).

<hr>

# Inspecting parts prior to assembly

Carefully inspect the electronics boards for the following:

- Bent pins (all pins must be perfectly straight and perpendicular to the PCB). Use a long-nose pliers to carefully bend them back.

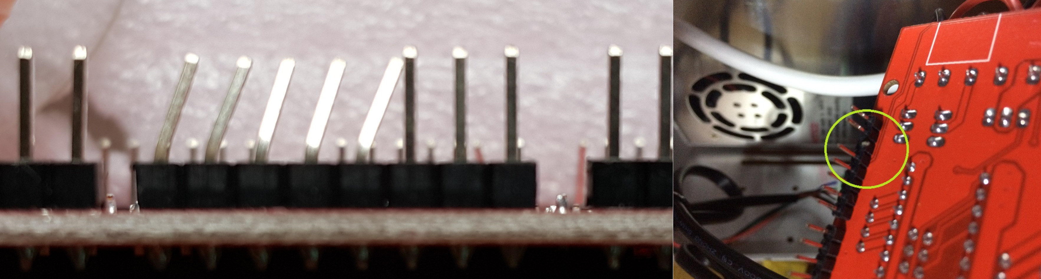
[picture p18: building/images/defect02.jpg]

- Check for short circuits between pins. In the picture below solder bridges appear to short tracks and pins; note however that the solder bridge is on top of the conformal coating, so it will not result in a short.  If you do have shorts carefully remove and if necessary re-flow the solder.

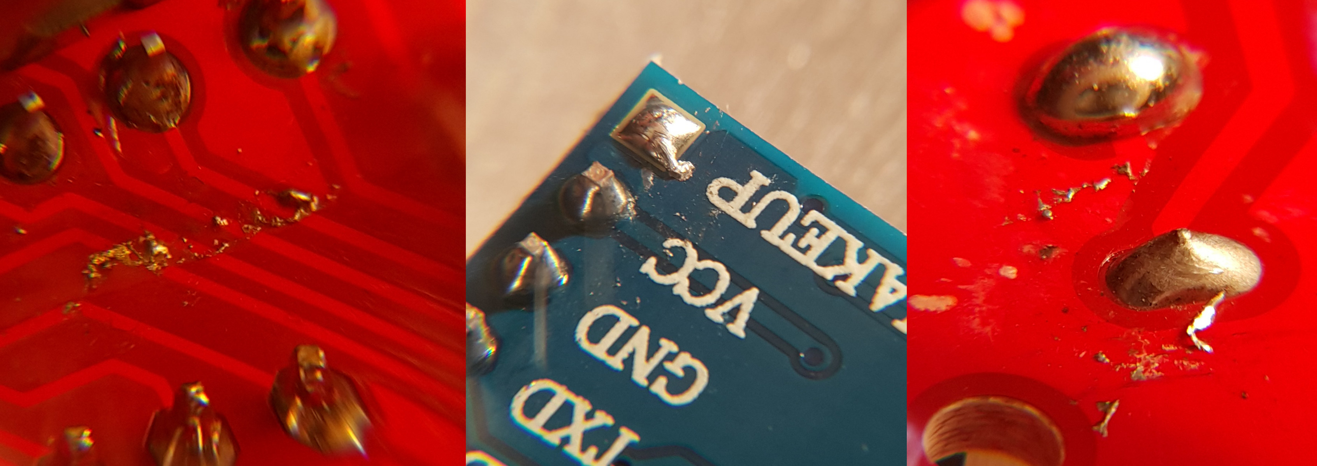
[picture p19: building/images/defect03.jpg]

- Check for broken tracks. Hairline cracks are very hard to spot, obviously broken tracks such as caused by scratches are easier to spot

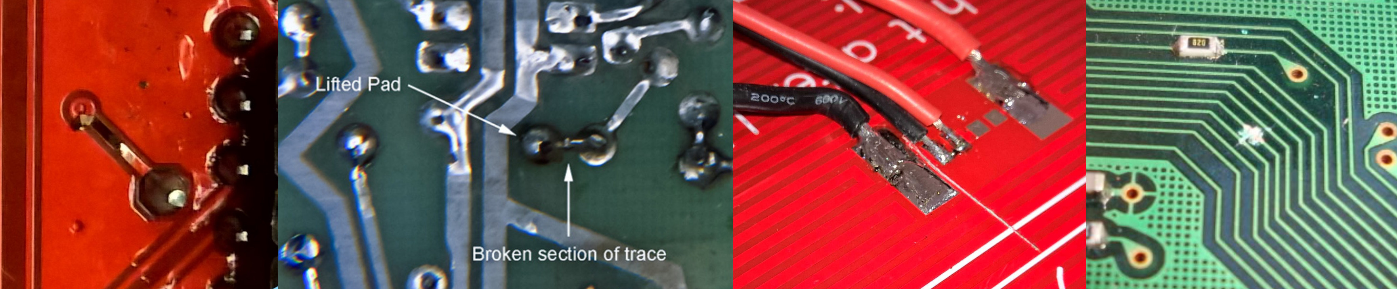
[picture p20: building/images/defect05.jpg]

- Check for the RAMPS board MOSFETs not touching anything. The three big shiny components are the MOSFETs.  They may be bent or otherwise touching some other wire or electronic component. Carefully bend them upright and clear of anything else.

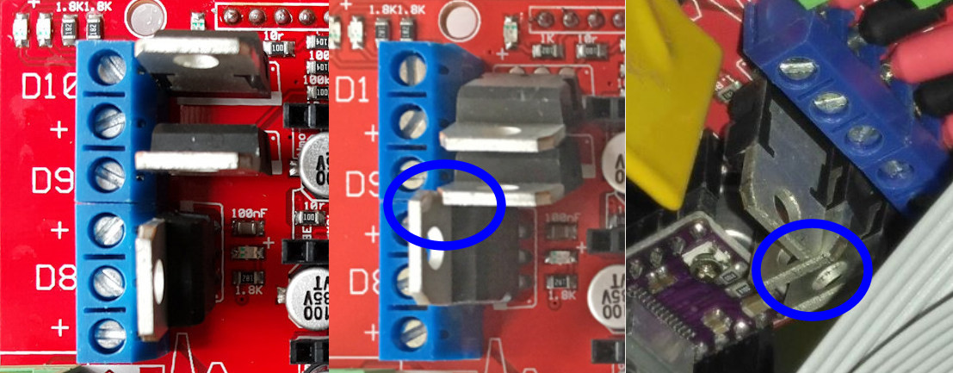
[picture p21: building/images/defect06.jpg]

- Dry joints or damaged solder joints. These are hard to fix, get an expert to do this or buy a new board.

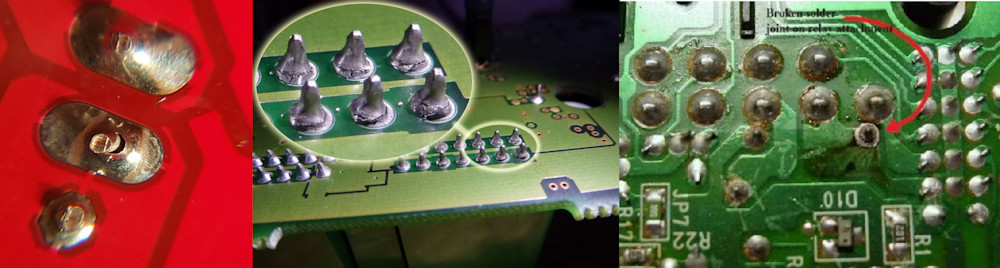
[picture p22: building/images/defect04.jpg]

- Check seating for all connectors.  In my printer the Molex connector pins slid back out when pressed from the front.  This could result in no or intermittent contact.  Carefully inspect both sides of the connector to ensure that all pins are making good contact.
- Check the resistance of the thermistors, for the standard and Diamond head, as well as the heated bed the values should be between 90 kOhm and 100 kOhm (pins not connected to the electronics) at temperatures of 20-25 deg C. Once connected the thermistor is in parallel with a 4.7 KOhm resistor, and the 100 kOhm (at room temperature) will not be measurable.  The hot end thermistors are connected to the small white wires in the Model connector.  The heated bed thermistor is connected to the two thinner wires on the inside of the heated bed PCB.
- Check the resistance of the heated bed, it should be around 1.2-1.5 Ohm.
- Check the stepper motor phase resistance. Connect the stepper motor cable (6-pin white connector on the one side and 4 pin black connector on the other side).  The motor phase resistance is measured between the two left-most and the two right-most pins.  The phase resistance should be of the order of 1.3 to 1.7 Ohm.

Inspect the mechanics and other hardware:

- Presumably the aluminium parts are accurately cut to size - this is the main reason to buy the Trium: the excellent metal frame.
- Check the length of the GT2 belts, some users reported they barely fit.
- Check the length of the Bowden/PTFE tube, it could be [too short](http://trium3d.proboards.com/thread/13/anybody-successfull-print-new-trium?page=6): on one printer the PTFE tube  is too short and at x=-90 y0 z0 it pulls up the head.  The solution is to use longer (1 m) tubes.

# Arduino and RAMPS boards

## Arduino

The Arduino board can be powered in one of three ways: (1) 5 V via the USB, (2) 7-14 V via the Vin pin, or (3)  7-14 V via the round power connector on the board.  In this case the Arduino board gets 12 V power on its Vin pin  from RAMPS board (see the lower left corner of the RAMPS circuit diagram).  The power flows from the RAMPS 12 V input, through the MRF500 fuse and a diode to the Vin pin.  If the Arduino board only works on USB but not from the RAMPS board it may be a bent pin, blown fuse or some other disconnect.  You should be able to power up the Arduino using 12 V from the power supply into the round power connector.

## Firmware

Make sure to install the correct firmware for your hot end.  There are [two versions](https://emergin.net/support/): the E3D hot end version and the Trium hot end version.  The two different hot heads have different sensor parameters encoded in the firmware.  You may have to modify some variables in the firmware code.  Use the ino file downloaded from the E-Mergin web site, change variable and flash down to the printer using the Arduino IDE (latest available version).

Install the firmware as shown [here](https://www.youtube.com/watch?v=Rwoz79IAFwI&index=18&list=PLMmAHPJoXlL8cp_-7R_6Hdb887jVPCUp3) or [here](https://www.youtube.com/watch?v=sOojWpuci_o&feature=youtu.be).

When flashing the firmware you will get a [time-out message if](https://www.kickstarter.com/projects/873464596/trium-delta-3d-printer/posts/1772659) (1) if you have a bluetooth chip connected, (2) if the slicer is currently accessing the board, or (3) [the USB cable may not seat properly](https://www.facebook.com/groups/emergin/permalink/1865886796982413/).

If the Arduino IDE is installed, the necessary serial drivers should be installed as well.  On the forum and facebook page, the Trium users often refer to the `FTDI` driver to be installed.  The serial chip used in many (if not all) Chinese Arduino boards are in fact the CH340, see [here](http://www.microcontrols.org/arduino-uno-clone-ch340-ch341-chipset-usb-drivers/) and [here](https://www.youtube.com/watch?v=Ix4t-_RZ7NI).  It seems that the drivers are available [here](http://www.wch.cn/download/CH341SER_ZIP.html), but download at your own risk. On the [Trium forum](http://trium3d.proboards.com/thread/24/problems-recognizing-trium-usb-port) E-Mergin advises that the FTDI drivers be downloaded from [here](http://www.ftdichip.com/Drivers/D2XX.htm).

## Setting up the RAMPS board

(p38) The Trium uses the RAMPS 1.4. The following picture shows how the wires are connected.  The cable orientation are shown in the short colour bars for the inductive sensor, the endstops and the stepper drivers. For example, the black wire on the stepper cables should be on 1B. The complete wiring diagram is also shown below, showing the cable colour next to each connector.

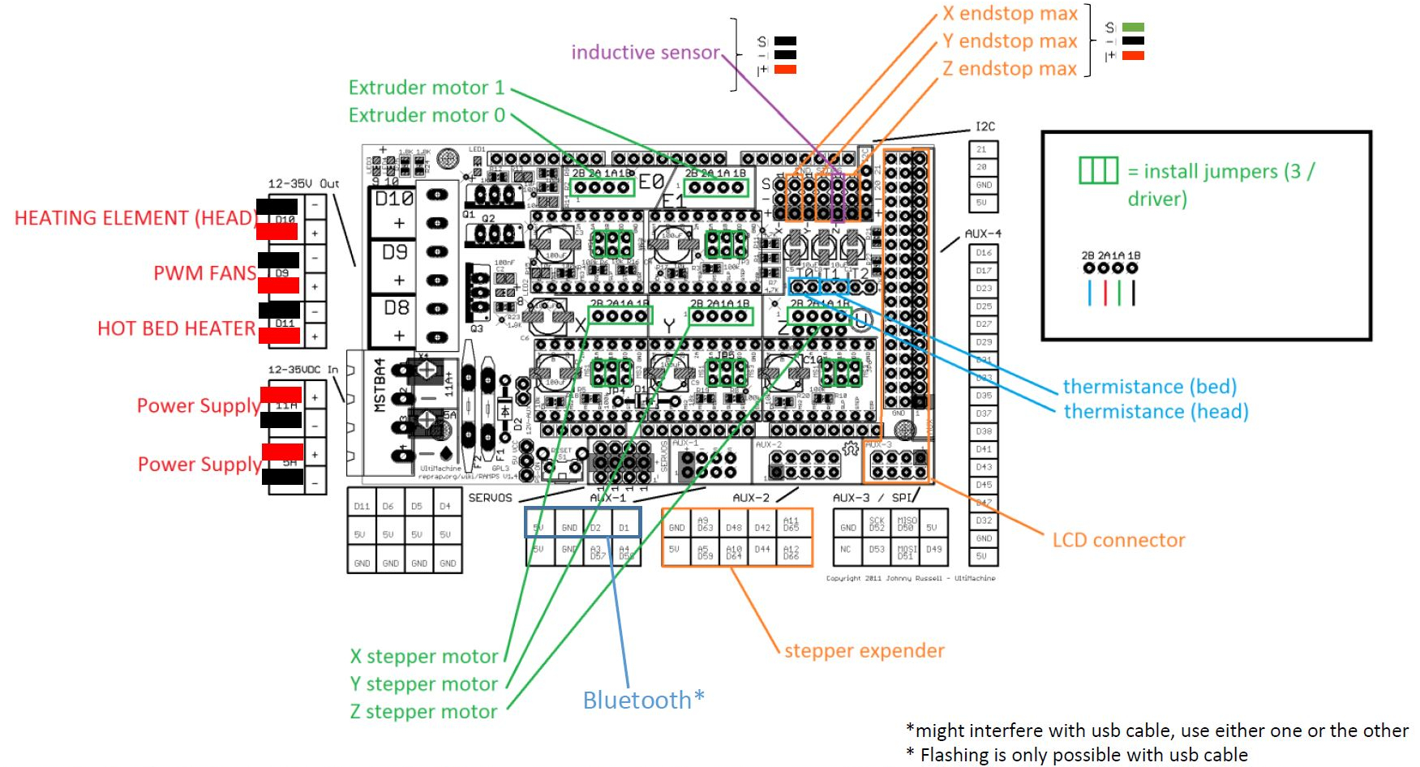
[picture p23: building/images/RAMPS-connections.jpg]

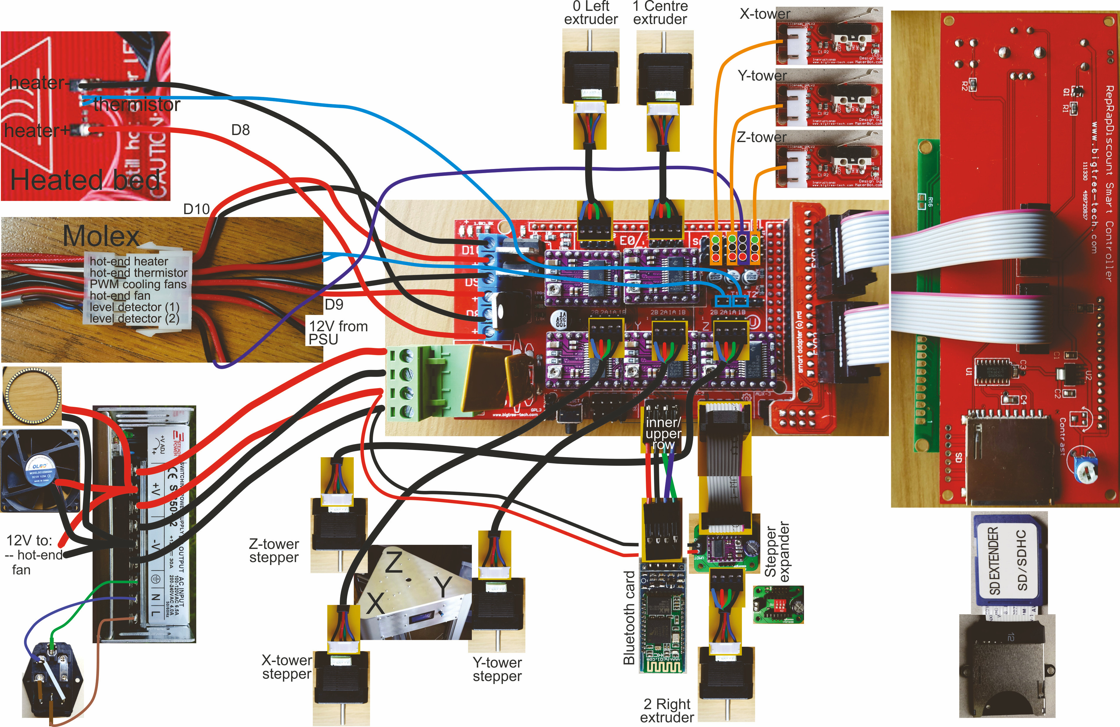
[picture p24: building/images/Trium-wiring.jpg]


(p18, p38) The RAMPS board requires jumper settings on (blue in the diagram below).  These settings determine the [number of micro steps](http://reprap.org/wiki/RAMPS_1.4). If the jumpers set it to a higher number of micro steps than supported by the driver it will operate at the maximum number of micro steps for that driver. The default is maximum micro stepping (all jumpers installed under drivers), which results in 1/32 for DRV8825. So set all three jumpers for each driver.
- the three delta stepper motors X,Y, and Z.
- E0 if only the standard head is used.
- E0, E1 and the extra stepper extender if the Diamond head is used.

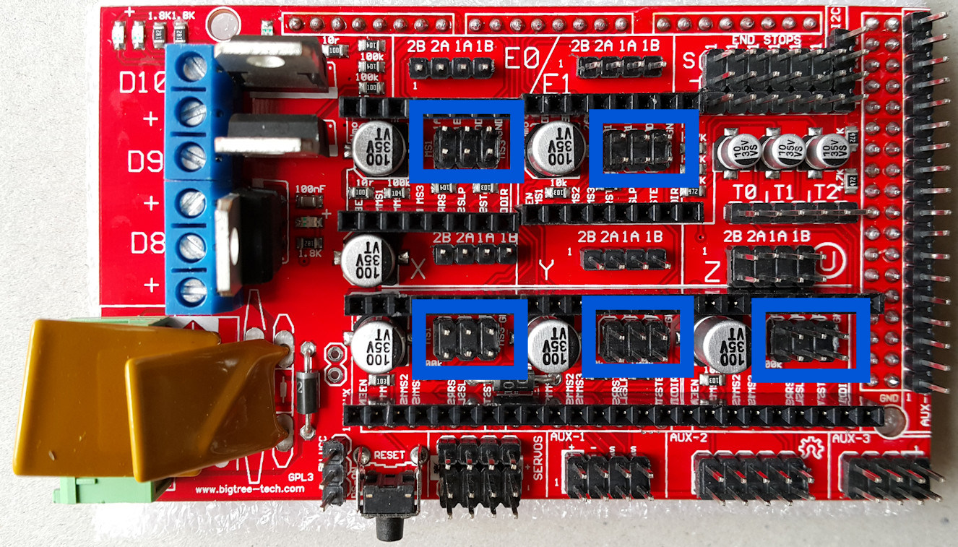
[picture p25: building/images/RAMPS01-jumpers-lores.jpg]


(p36) Before mounting the small driver PCBs, calibrate the stepper motor drivers by setting the potentiometers as detailed in the Manual (p36).  The 'Quick calibration' method is grossly inaccurate - only use this if you cannot use the more accurate method.

Optional:  It might be convenient to reset the Arduino from outside (with a switch or by a future wifi connection).  In order to facilitate resetting the Arduino later, I soldered two pins to the underside of the reset switch on the RAMPs board.  Any connection can be made to these two points later.  These two reset pins extend a little towards the stepper driver extended (for Diamond hot end users).

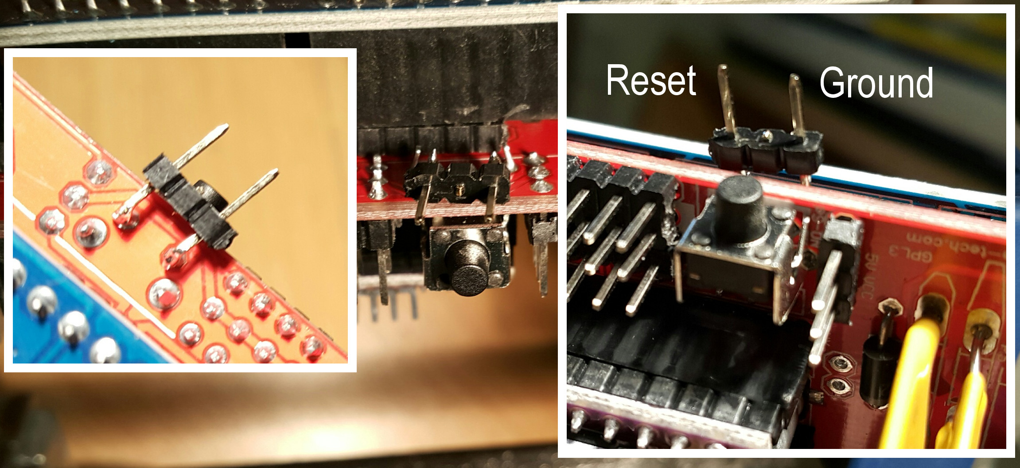
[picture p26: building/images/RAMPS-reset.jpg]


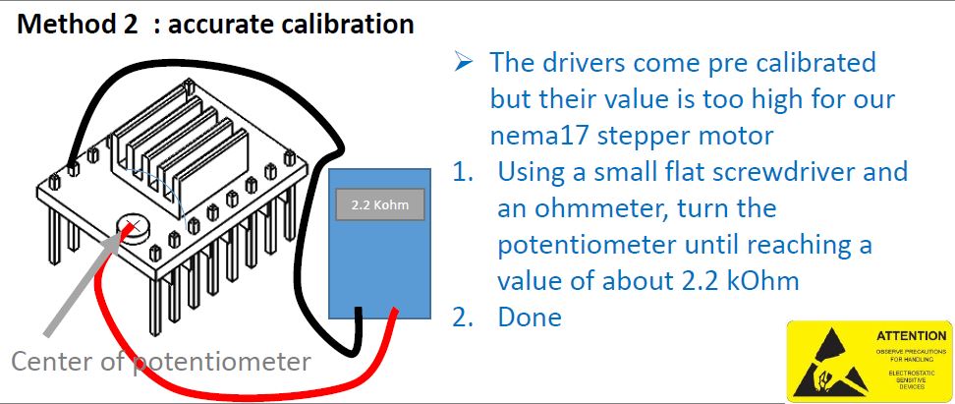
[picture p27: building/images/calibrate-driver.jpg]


Some users pointed out that it is difficult to set the value accurately. The PCB is small and one seems to have too few hands to do the task. The E-Mergin assembly video shows a technique to connect the multimeter to the screw driver.  The following alternative setup makes it trivially easy to set the trimpot.  Use a protoboard to fix the PCB position (it does not slide all over the desk).  Wire the ground pin (second pin) to the first multimeter using the protoboard. Use one hand to turn the pot and the other to hold the second multimeter lead.

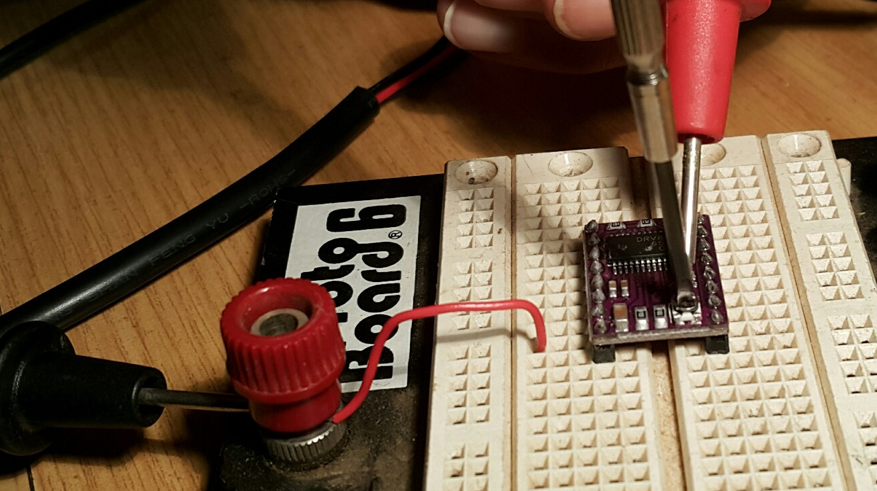
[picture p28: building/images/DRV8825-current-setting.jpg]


(p18) Insert the driver PCB in the orientation shown in the next picture (before and after heat sinks are stuck on).  Stick the small self-adhesive heat sinks on top of the IC on the driver PCBs.

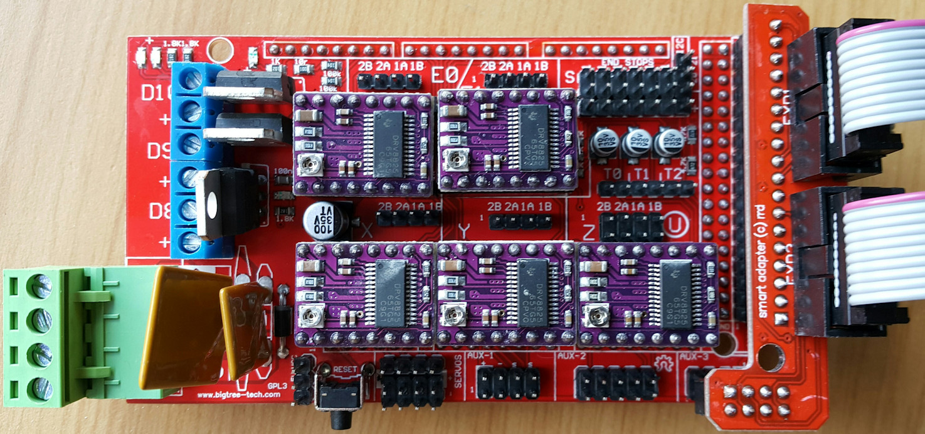
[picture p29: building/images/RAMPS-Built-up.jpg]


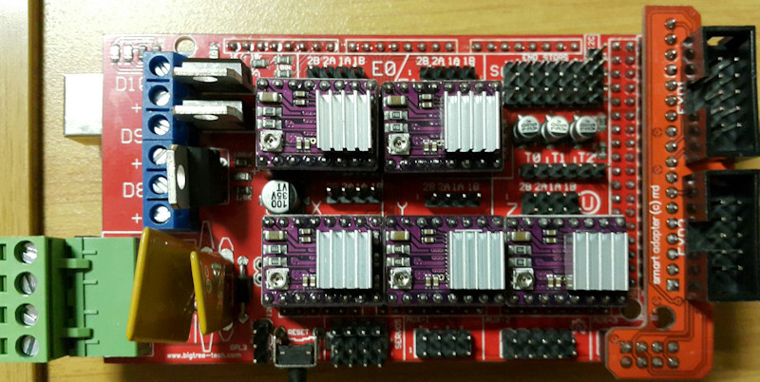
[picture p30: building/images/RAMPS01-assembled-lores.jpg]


(p18) If you have a Diamond hot end, assemble the third extruder driver (used in addition to the five other stepper motor drivers on  the RAMPS board). Set all three switches to 'on' position (this is the same as inserting all three jumpers on the RAMPS board).  Insert the driver with heat sink as shown in the below (heat sink not yet mounted).  Mount the power supply cable into the terminal block with the black wire on ground (GND) and the red wire on (VMOT) (if necessary cut of the ferrules to expose just the copper wire).

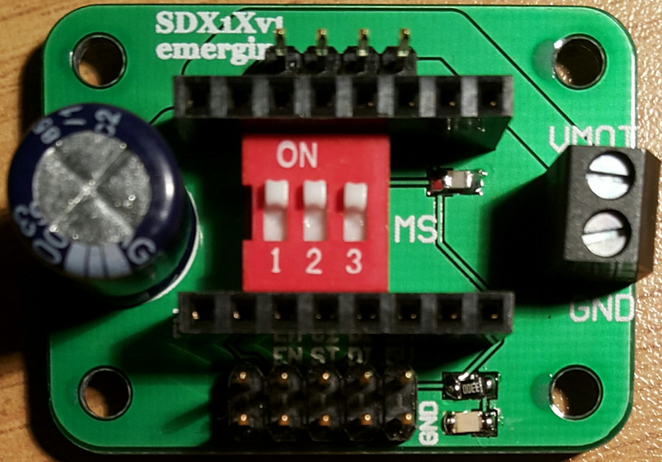
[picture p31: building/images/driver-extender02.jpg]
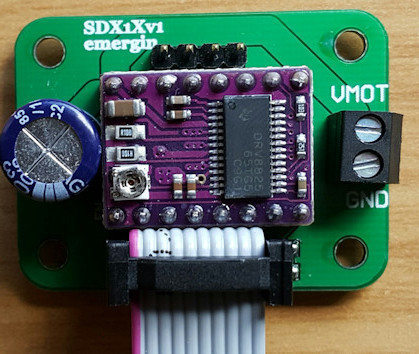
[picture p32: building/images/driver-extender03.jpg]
 

[This tutorial](http://3dtek.xyz/blogs/technical-docs/18982427-not-another-ramps-tutorial) describes wiring the RAMPS for another printer.  It does not fully apply to the Trium, so read with care.

[MiR advises](http://trium3d.proboards.com/thread/67/notes-building-trium-standard-diamond) to print out a fan holder and to mount the fan directly to the Ramps Board. He used  [this thing](www.thingiverse.com/thing:166045)  (You will need to use 3mm screws, 4mm screws will not fit).  Later found [this](www.thingiverse.com/thing:211672) one, has some small improvements.  See also the customiser [here](http://www.thingiverse.com/apps/customizer/run?thing_id=166045&code=b8a1480ff8c69a94a20b4d2d0528a997).

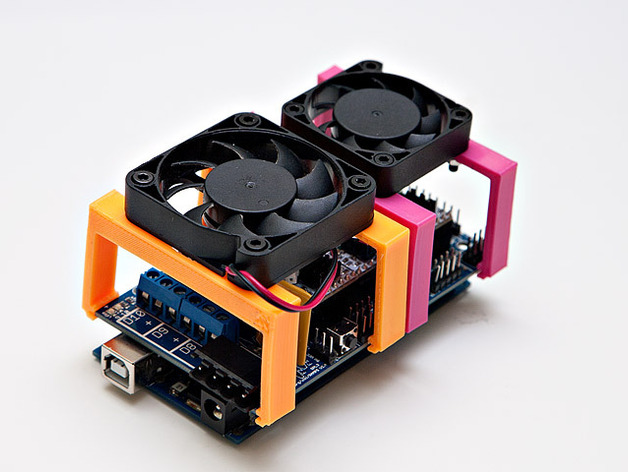
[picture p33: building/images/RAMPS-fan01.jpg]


## Integrating the Arduino and RAMPS boards

(p18) [MiR has an excellent suggestion](http://trium3d.proboards.com/thread/67/notes-building-trium-standard-diamond) to first integrate the electronics and test it stand-alone, before building it into the Top Plate Assy. Do the following on a non-conductive surface (not on the aluminium Top Plate):

- Place the RAMPS board on top of the Arduino board, carefully check that all the RAMPS pins are properly aligned with the Arduino headers (adjust the headers and pins if necessary). If you are certain that all pins align, gently press the two boards together.  The RAMPS board pins should be carefully forced all the way into Arduino sockets, don't leave gaps where pins are visible.

- Connect the LCD small L-shaped adapter board to the RAMPS, connect the two ten-pin ribbon cables to the adapter and to the LCD board.  The ribbon cable connectors have keys, and and only plug in in one orientation.

- Connect the USB-Cable (Extender) to the Arduino Board.

- Connect your computer via the provided USB Cable to the plug of the USB-Cable (Extender).

- Install firmware on Arduino as described in the manual. See also  [here](https://www.youtube.com/watch?v=Rwoz79IAFwI&index=18&list=PLMmAHPJoXlL8cp_-7R_6Hdb887jVPCUp3) or [here](https://www.youtube.com/watch?v=sOojWpuci_o&feature=youtu.be), or see [LMGTFY](http://lmgtfy.com/?q=download+RAMPS+firmware).

After flashing (or when you press the reset button on the side of the RAMPS board) you should see an error message on the display, that's OK, we have not yet connected any sensors so the safety features of Marlin kick in (see picture below).

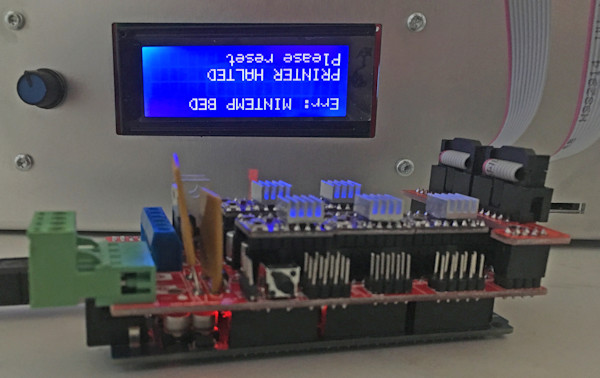
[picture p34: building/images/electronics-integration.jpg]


Disconnect the USB connector from the Arduino board and remove the LCD ribbon cables.

# Top Plate Assembly

If you plan to use the Diamond head punch out the two additional extruder holes on one of the triangle sides (the centre hole should already be open).  Also, if you are planning to use three Trium horizontal spool holders, punch out the three holes in the corners on the top plate.  Some people prefer to use [vertical spool holders](https://www.thingiverse.com/thing:2001034), so consider your options.  My printer came supplied with only one spool holder (even though I ordered the Diamond nozzle).

(p16) Mount the extraction fan such that the air is forced *into the cavity* (arrow pointing inwards, or fan label is visible when mounted).  The logic of blowing into the cavity, instead of extruding air from the cavity as for PCs, is probably to prevent hot air from the printing volume (between the towers) being sucked into the Top Plate cavity.

[MiR](http://trium3d.proboards.com/thread/67/notes-building-trium-standard-diamond) and [Jean Marc Cierniewski](https://www.facebook.com/groups/emergin/permalink/1871767846394308/) found that the fan is very loud, so some form of damping (rubber, silicon, cork) between the fan and the frame may help reduce noise.

(p16) Mount the power switch. My printer is connected as shown below; where green is earth, blue is neutral and brown in live. This is different from Trium instruction, be careful.

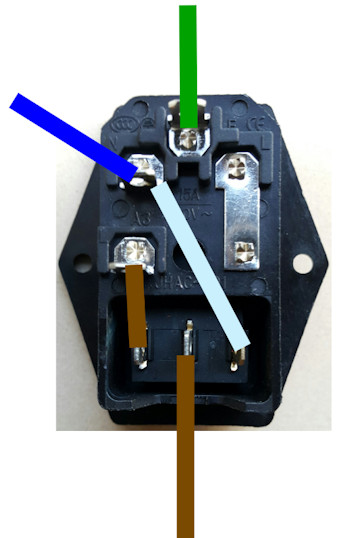
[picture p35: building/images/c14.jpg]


(p16) Mount the USB cable.

(p37) On the SD-card extender, remove the small plastic guides between the copper connections.

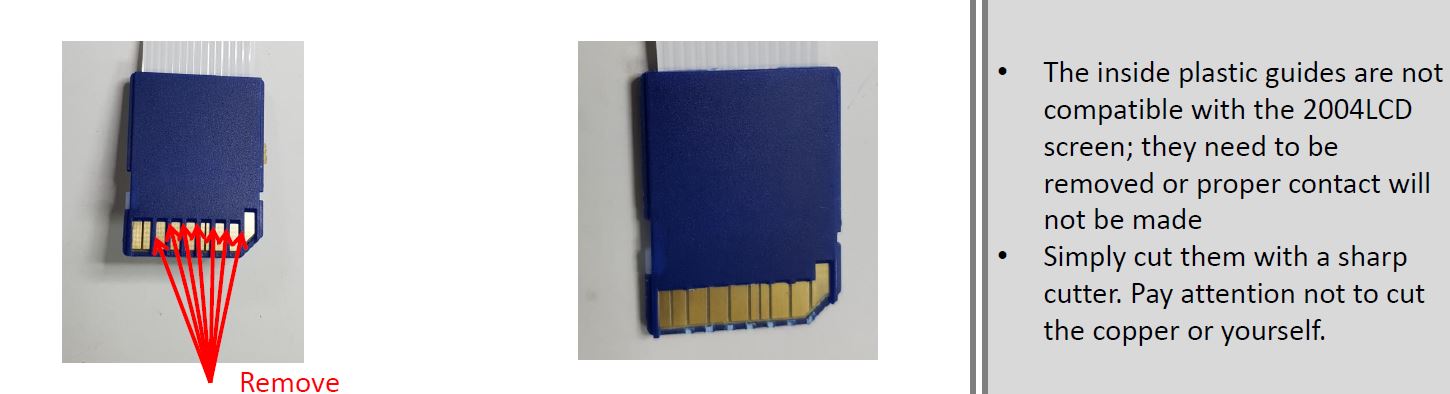
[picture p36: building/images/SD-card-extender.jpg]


(p17) Mount the SD card extender.  Before you mount the SD card extender, pass the USB extension cable below the SD extender, behind the two pillars. In my case I mounted the SD extender pillars with Loctite and was unable to unscrew the pillars - now it must lie on top.

Before moving on, test the height of the SD card extender to confirm easy card access through the hole in the Top Plate.  In my case the pillar was too high and hence the extender sits too high relative to the hole.

If you can also confirm that the SD card extender orientation is the right way up (I think mine requires the card to slide in upside-down).   Keep in mind that at this stage the Top Plate is upside down.

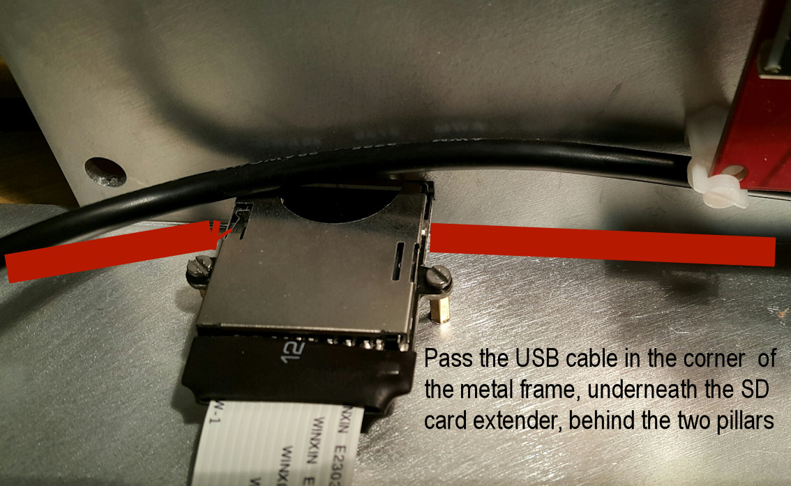
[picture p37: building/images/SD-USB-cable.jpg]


(p17) When mounting the LCD board, initially screw in only one spacer: the one bottom on the side of the SD-Card.  When you now assemble the display it stays in place, it is fixed on one side by the spacer and the other side by the switch spindle that goes through the hole. You can now easily add the other spacers, starting by the 2nd one on the bottom.  In the picture below note that the PCB corner fits into the gap at the top of the mounting pillar. The pillar must be rotated to be at 45 degrees with the two PCB edges.

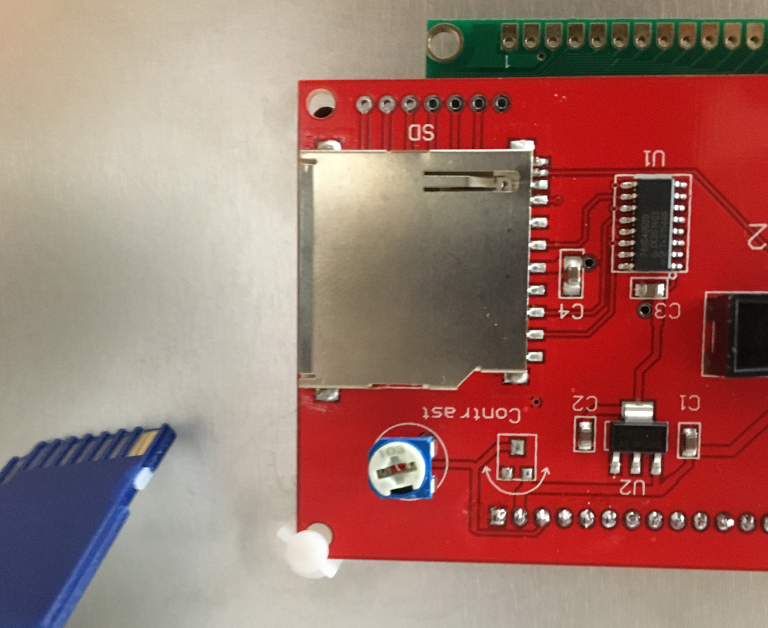
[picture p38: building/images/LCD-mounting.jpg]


(p19) Mount the power supply. Mains power can be lethal, disconnect all power leads before working on these wires and make very sure that the wires are connected correctly.

<font color="red"> *When wiring your power supply, make very sure that the brown and blue wires never touch anywhere else than on the switch and on the L and N terminals on the power supply.* </font> If for some reason you suspect that the cable is faulty, have it fixed by a knowledgeable person.  E-Mergin has done the right thing by properly covering the electricity leads with insulation material, but the flat shiny bar on the right-hand side of the switch is also at live potential and *it is not covered*.  Please be very careful.

On the side of the power supply there is a switch where you must select the voltage (115 or 230V) for your country (mine was preset at 230V). Mount the power supply in the Top Plate as shown in the Manual (p19).

Connect the 220V mains cable between the on/off switch and the power supply, being careful to follow the brown/blue/green colour convention.  If you wish, you can zip-tie the internal power cable down to the side of the power supply, just do not block the air vents at the bottom of the supply.

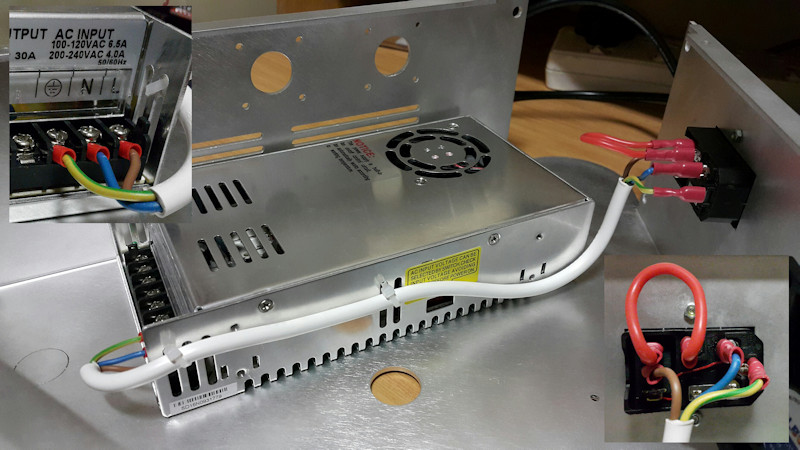
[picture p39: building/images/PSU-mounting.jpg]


Optional - your choice: The next picture shows how the neutral and ground (negative/black) wires are connected to the case (note the thick bare copper wire going underneath the terminal block, firmly screwed to the case).  I also added a terminal block for the large number of wires connected to the power supply.  Note, however that the terminal block will interfere with the horizontal spool holder bolt extending below the top.

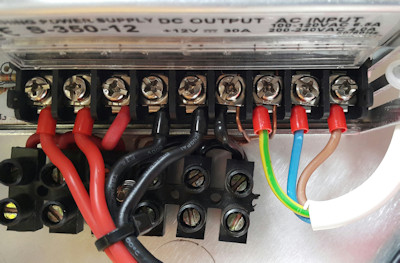
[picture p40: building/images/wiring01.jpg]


**Test the power supply output voltage before connecting anything to it!**
At this point you should have a working power supply.  To verify the supply operation and voltage, connect the printer to the mains supply and switch on.  Measure the voltage on the power supply output between the - and + terminals.  It should be around 12V; if not, adjust the voltage by turning the potentiometer on the left side of the power supply.

Switch off the power supply and <font color="red">**disconnect the power cable**</font> from the printer.

## SD Card not working

If the SD card is [not detected](https://www.facebook.com/groups/emergin/permalink/1870864693151290/) try [these steps](https://www.facebook.com/groups/emergin/permalink/1869330273304732/):
-  Insert the SD card before power on so that the printer boots with the SD card in place.
-  Experiment with different SD cards - different users have different experiences with small, large, new and old cards. Find one that works.
- Check your SD card is using the FAT file format.
- Verify that the SD card extender loom is well connected into the LCD board.
- Verify that the SD card extender mount screws are not too tight
- If the printer still doesn't see it, try opening SDFatConfig.h go to the 74th line:	`#define SPI_SD_INIT_RATE 5`. Change it to read: `#define SPI_SD_INIT_RATE 6`. Then re-flash the firmware.

##  Mounting the Arduino/RAMPS boards

(p18, p19) When mounting the Arduino/RAMPS and extender boards, [MiR suggests](http://trium3d.proboards.com/thread/67/notes-building-trium-standard-diamond) the following:

- Take two mounting pillars and screw in the two spacers that are on the wide side of the Arduino PCB, on the side facing the edge containing the extruder holes.

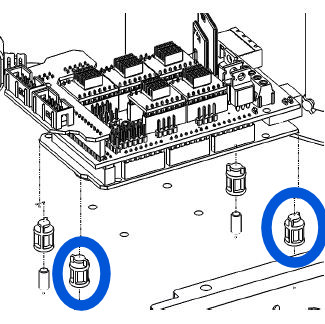
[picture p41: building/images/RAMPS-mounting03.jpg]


- If you have Diamond head prepare the two mounting pillars for the extension board.
- Turn the case so that it stands on the side with the hole(s) for the extruders. The two Arduino and two extender mounting pillars should now the at the lower edges of the boards.
- Align the mounting pillars so that they are roughly angled 45 degrees. Now you can slide in the boards, they stay in place thanks to gravity.
- Finally assemble the missing mounting pillars.



## Wiring and EMC and interference prevention

[mikeeitel proposed](http://trium3d.proboards.com/thread/51/emv-protection) some measures to lower interference. I added a few additional recommendations. These are:

- Route the LCD cables below the Arduino (between the Arduino and the aluminium case), to prevent interference from the stepper drivers into the LCD cables (the ribbon cable does not have screening).  Do the same for the stepper driver extender card.  The stepper driver chips feed high frequency noise into the heat sinks, which then radiates EMI signals (perhaps one can ground the heat sinks?). Keeping the LCD and other wires away from the stepper drivers helps lower EMI interference. This picture shows the ribbon cables passing underneath the Arduino and stepper driver extender board.  It keeps the ribbon cables out the way and reduces the risk of EMI.  The added benefit is that the layout is cleaner with less cable clutter. Some users complained that the LCD screen shows gibberish - this is caused by EMI: the LCD should reset every 10 seconds, alternatively press the rotating button.



- Pull the bed heater cables and thermistor cables through different towers, to prevent noise interference with the temperature measurement.

- Route the stepper cables over the power supply and from there as straight as possible, and away from other cables, in right angles to the drivers.

- Try to keep the tower endstop switch wiring away from the stepper motor wiring.

- Mount a large (>10 microF, >20V) electrolytic capacitor and a 100-470 nF capacitor in parallel directly to the output switched power supply. Be careful with the electrolytic capacitor polarity, connect the + side to the + PSU terminal. Note that all three + output screws on the PSU are connected to each other, and all three - output screws are connected to each other, so one set of capacitors will serve for all three connections,

- Optional, but recommended: The enclosed aluminium case has reasonable potential for preventing the printer to radiate electrical noise and to protect the printer from outside interference.  However, just screwing them together does not always provide good electrical connection. Drill holes in the two Top Plate aluminium parts, and tightly screw the parts with a nice thick wire to the mains earth connection.  There some holes in the Top Plate assembly, so the assembly does not provide a perfect Faraday cage, but every little bit of screening helps.

- Optional, but recommended: Add an [EMI filter](http://www.ebay.co.uk/itm/3900W-EMI-18A-High-Frequency-Power-Filter-Board-DIY-Kits-For-Speaker-Amplifier/262372720254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) to the mains power leads. This filter should be able to provide the current required by the printer. This EMI filter is not the same as a surge protector - the surge protector protects your printer against lightning. The EMI filter suppresses high frequency noise spikes (household appliances and lights switching on or off) on the power lines.



- Optional, but recommended: There are three Pulse Width Modulation (PWM) outputs on the RAMPS board.  These PWM signals (8 A for the bed heater and 3 A for the hot-end heater) are switched fully on and fully off in variable on/off time ratios (hence 'pulse width') such that the low frequency average provides the required power level. These currents are  switched on and off in very short time periods, leading to considerable high frequency content (30-40 MHz).  These signals on the PWM wires can/should be filtered to remove some of the very high frequency content that might cause interference in radio or other electronics. [Ferrite components](http://eemc.nl/nl/pdf/EMI%20Suppression%20with%20Ferrites.pdf) absorb high frequency magnetic fields and thereby suppresses the EMI.  At large DC currents the magnetic circuit saturates and the filter becomes less effective. The [correct use of ferrites for DC carrying conductors](http://educypedia.karadimov.info/library/Use%20of%20Ferrites%20in%20EMI.pdf) is as shown below, where the two conductors must follow closely the same path through the ferrite component. Additional turns through a core will provide multiples of peak impedance, furthermore, the impedance peak shifts to a slightly lower frequency. In my printer I used a ferrite ring and was able to push two windings through the ring (this shortened the lead, so I would have to lengthen the leads). Keep the red and black wire as closely together as possible so as to create a net-zero magnetic field at DC.  Solder a 10-100 nF capacitor on the one side of the ferrite wires.  Make two such filters: connect the capacitor-side of the filter to the connector for D8 (bed heater) and D10 (hot-end-heater). For more information see [here](http://www.a-m-c.com/download/support/an-023.pdf), [here](http://www.allaboutcircuits.com/technical-articles/choosing-and-using-ferrite-beads/), [here](http://www.skyworksinc.com/uploads/documents/202378A.pdf), and [here](http://www.pcsilencioso.com/cpemma/pwm.html).



- Optional: If you can solder two wires to the RAMPS reset switch, mount a switch somewhere on the frame.

- Optional information: The RAMPS board has two + (positive supply) input screws and two - (negative supply) input screws.  The negative screws are connected together internally and form the ground for the electronics.  However, **the two positive screws are not connected together)** each positive input serves another part of the electronics. Analysing the RAMPS circuit diagram, it is evident that the left-most/top positive supply +12V2 feeds directly into the bed heater MOSFET and appears not connected to any other component on the RAMPS.  The +12V2 has no decoupling capacitor on the input or MOSFET output.  The third connection from the left/top is labelled +12V and feeds the rest of the electronics, the PWM cooling fans and the PWM hot end heater element.  This input is decoupled with a 100 nF and 100 microF capacitor near the input connector. Furthermore, each driver carrier +12V is also decoupled with 100 microF. So there is probably no need to further decouple the +12V supply on the RAMPS board.

[Mir suggests](http://trium3d.proboards.com/thread/67/notes-building-trium-standard-diamond) that it would make sense to perhaps build up the print head now and do some testing of the electronics together with the print head.  But both MiR and me instead went on constructing the extruders.

**Checking the driver calibration**  Now would be a good time to measure the true reference voltages on the stepper motor drivers, as part of validating your driver calibration.  The voltages (relative to negative/back) on the centre of the potentiometer should be in the range 0.85 to 0.95 V.  When I measured these values in circuit, all the voltage levels were below 0.8 V, even as low as 0.75 V.  All six drivers calibration was re-adjusted to 0.85 V, perhaps on the low side - we'll see later if this was too low.

## Main case fan

Diamond head users: The main case fan can be connected to the stepper extension board because it is nearest the fan. Connect the red fan wire to the `VMOT` terminal and the black fan wire to the `GND`.

Standard head users: The main case fan can be connected to the green terminal block on the RAMPS board because it is nearest the fan. Connect the red fan wire to the + terminal and the black fan wire to the - terminal.

The main case fan must force air into the cavity. I think is is because if the fan extracts air out of the cavity, the cavity inflow will be the hot air from below.  After connecting check the airflow to confirm that the fan forces cool outside air into the cavity.

In my build, I extended the fan wires to connect directly to the power supply. It is neater and just feels better.

# Extruders mounted in the Top Plate
## Extruder assembly

Remember that the while you are working on the Top Plate, it is upside down, so you must mount the extruders upside down!



Trium uses a Chinese variation of the GeeeTech MK 8 extruder (something like [this](https://www.aliexpress.com/store/product/42HD4027-01-Aluminum-3D-Printer-Extruder-kit-Set-w-NEMA-17-Stepper-Motor-For-1-75mm/333670_32663281335.html), [this](http://www.icstation.com/left-hand-extruder-aluminum-frame-block-printer-p-6326.html), or [this](https://www.aliexpress.com/item/2pcs-lot-Aluminum-block-DIY-kit-Left-hand-For-single-nozzle-MK8-extruder-extrusion-printer-head/32575822076.html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), or [this](http://www.thingiverse.com/thing:1386402)).

Optional: Measure the stepper motor phase resistance before mounting. Connect the cable (6 pins white -- 4 pins black) to the motors and measure the motor phase resistance between the left-most two pins and right-most two pins on the black connector.  The phase resistance should be close to 1.65 Ohm.



[MatterHacker's extruder tutorial](http://www.matterhackers.com/articles/extruders-101:-a-crash-course-on-an-essential-component-of-your-3d-printer) provides a good introduction to extruders.  [This page](http://reprap.org/wiki/Extruder_assembly) may be helpful in assembly - but the wiki describes hardware where the hot end is integrated with the extruder. The procedure described in the wiki differs slightly from the Trium procedure (stop at step 8 in the wiki procedure).

In the wiki Step 4, there is mention of a M4 gasket (washer?) (item 9 in the wiki figure).  **This gasket is missing from the extruder kit as delivered.** This gasket is quite important because without it, the pulley is fact touching/rubbing directly on the hinge part. The friction between the pulley and the hinge negates the presence of the bearing.  Please add your own M4 washer between the gold-coloured part and the pulley/bearing. Thanks to BillB for pointing out that the black screw belongs under the spring.

p20 Trium build:
- Step 1: Screw in the black screw (1) into the hole in Part A, *from below*. The screw tip of (1) will eventually hold the bottom end of the spring secure.
- Step 2: Trium mounts the stepper motor and extruder components on both sides of one of the Top Plate walls (p20).  Locate the stepper motor on the inside with the connector to one side (if the connector is facing down it is difficult to plug in the cable).  Place Part A on the outside and screw in the two bottom screws (2) and (3), into the bottom holes of the stepper motor.
- Step 3: screw (4) into the stepper motor in the top-tight hole.
- Step 4: mount the hobbed gear (Part C) on the motor spindle. Ensure that one of the two grub screws seat into the flat surface on the motor spindle.
- Step 5: screw the (missing) M4 washer, bearing and pulley into Part B.



- Step 6: screw the large stainless steel screw (6) into Part B.
- Step 7: fix Part B onto Part A by screwing (7) into the top-left hole in the motor.  This screw should not be tightened, to allow a swivel movement of Part B around (7).
- Step 8: slide the small stainless steel screw  (8) into the spring.
- Step 9: place the bottom of the spring over (1) and set the bottom of screw (6) into the top of screw (8).  The spring should now press against Part B.  The tension in the extruder (pressure of the pulley onto the hobbed gear) is adjusted by turning (6).
- Step 10: When installing the Bowden tube see  [handling of the Bowden tube](reprap.org/wiki/Diamond_Hot end).

After assembly you will be left a a few unused components that came with the kit.

Connect the stepper motors with the appropriate connectors on the RAMPS PCB.  Make a note of which extruder number E0, E1 or extender is connected to which extruder motor. Perhaps it would be easiest to remember that the right -hand-side extruder is E0, and so on.  When stepper extender is plugged on the small PCB the blue wire must be on the terminal or  right-hand side when viewed for reading the text.

.



## Further notes on the extruder

### Extruder unable to push filament

Tighten the screw above the extruder until it grips. But don't tighten too much, it may force the PTFE tube to pull out at the extruder or hot end if the hot end somehow blocks the filament.

The Marlin firmware prevents the extruder motors to turn if the hot end temperature is below 175 C.  This is to prevent cold extrusion. You can temporarily override this with the gcode `M302 P1`.

### Printing with flexible filament
The standard MK8 extruder as delivered on Trium cannot print flexible filament: the output coupler does not bring the Bowden tube close to the filament hobbed/cob gear.  Some mechanism is required to prevent the filament from buckling under extrusion.  The alternative options were presented thus far:



The solutions are from left to right:

1. [Andreas Pfeifer](https://www.facebook.com/groups/emergin/permalink/1867202580184168/) [here](http://www.thingiverse.com/thing:2035413) describes an adapter by KnoxD that fits to the extruder.
1. The adapter described [here](http://www.thingiverse.com/thing:1386402)  fits between the entry into the Bowden tube and the extruder cog wheel.  It is a very tight fit, the designer advises that the work piece be sanded to make it fit. **The width of this Thingiverse part  is too wide**, it should be 2 mm narrower for the extruder used in the Trium.
2. [Rajaa Kahel](https://www.facebook.com/photo.php?fbid=703445856496900&set=pcb.1857616977809395&type=3&theater)  recommends to replace the output coupler with a [coupler](https://www.aliexpress.com/item/2Pcs-Pneumatic-Fittings-PC4-M6-Bore-4-3mm-For-4mm-PTFE-Tube-connector-Coupler-Feed-inlet/32633859496.html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) inside diameter 4 mm hole, which allows the PTFE tube to push through all the way close to the hobbed gear. Another Trium user tried this and found that the tube slid out. Use [this](http://www.thingiverse.com/thing:2035468) to prevent release.
3.  Janlu's solution is shown [here](http://trium3d.proboards.com/thread/23/flexible-filaments)

### Noise dampers on the extruder
Trium users discussed the use of noise dampers on the stepper motors for the tower motors.  There is room in the tower for these dampers on the XYZ motors.  The mounting shown below allows only two mounting screws or the front and two on the back sides.  However, for the extruders, the motor mounting screws also provide mounting integrity for the extruder. So unless the extruders are really noisy, it would be best to avoid dampers here.



### Filament cleaner
A filament cleaner keeps dust and plastic particles out of the Bowden tube, nozzle and print.  You can use a [makeshift cleaner](https://www.facebook.com/photo.php?fbid=703445856496900&set=pcb.1857616977809395&type=3&theater) using a sponge to clean the filament. See also [here](https://www.facebook.com/groups/emergin/permalink/1868165253421234/). Locate the filament cleaner as close to the extruder as possible.  There are also [filament cleaners on Thingiverse](https://www.thingiverse.com/tag:filament_cleaner).



None of the above filament cleaners cleans the filament after passing through the extruder. Small fragments of filament waste could result from the extruder gear damage to the filament. Is this a problem?

### Filament lubrication
Filament lubrication on the filament is somewhat  controversial. Some insist that lubrication should never be used, because the teflon tube has sufficiently low friction.  Short radius bends and (filament) dust in the tube may increase friction (in both cases rather rectify the cause).  Some printer users advise that a small amount of lubrication solved their printer problems. Use oil with a [high smoke temperature](http://www.clovegarden.com/ingred/oilchart.html); commonly used oils are light mineral oil, refined canola oil, refined corn oil, or refined olive oil.  The key consideration is to use lubrication sparingly. For more information see the web sites [here](https://ultimaker.com/en/community/4483-lubricating-the-bowden-tube), [here](https://ultimaker.com/en/community/3110-trouble-making-soft-pla-prints#entry14759), [here](https://www.thingiverse.com/thing:48646), [here](http://forums.deltaprintr.com/index.php?threads/to-oil-or-not-to-oil.312/), [here](http://forums.deltaprintr.com/index.php?threads/to-oil-or-not-to-oil.312/), [here](https://www.3dhubs.com/talk/thread/oiling-pla-stop-jams), and [here](http://forums.reprap.org/read.php?1,286062)

There are several possible methods to lubricate the filament:
- Place a drop of oil on the dust filter sponge.
- Dip the filament tip into the oil and allow to drip excess. Print a skirt first to avoid excess oil in the work piece.
- Wet a sponge/cloth with oil and lightly wipe the first 10 cm of the filament.  Print a skirt first to avoid excess oil in the work piece.

### Filament grinding
Grinding is a considerable risk for softer filaments, but can also occur on PLA. Read [here for more information](http://support.3dverkstan.se/article/23-a-visual-ultimaker-troubleshooting-guide#grinding):   Grinding happens  when the motor tries to push the filament through the nozzle but for whatever reason it starts to slip on the filament and instead grinds the plastic down. The more it grinds the filament the less grip it is able to get and very soon it will not be able to move the filament neither in nor out. Grinding also creates filament dust that may enter the Bowden tube, leading to increased friction.  Grinding should be minimised by finding the correct balance between the hobbed gear pressure on the filament (adjust the extruder spring) and the stepper motor current limit.  By limiting the motor current the stepper motor will skip back *before starting to grind the filament down*. When this happens you will hear a *tock* sound and the feeder wheel will spin in reverse for about a quarter turn.  We can control the motor current by controlling the reference voltage on the DRV8825 driver. Optimise the combination of spring and current settings as follows: adjust the extruder spring to ensure good plastic flow under normal printing conditions. Once the optimal spring setting is found, while extruding against resistance (i.e., cold hot end) adjust the reference voltage (hence motor current) to force until the motor tocks/clicks before grinding occurs.

grinding

### Changing filament

In your favourite printing software (or the LCD) you go into manual mode and heat up your hot end to about 190°C. When this temperature is reached, you release pressure from your extruder by pushing its arm down. Then pull the filament out with your other hand. Then you can fiddle new filament into the extruder and push it down until it reaches the hot end. In manual mode of your printer software, now extrude until the colour is clearly this of your new filament without bits of your previous one. To be on the safe side, you should also print a bigger brim for your next model to see if there was any old filament left in the nozzle. See [here](https://www.facebook.com/groups/emergin/permalink/1866813056889787/) and [here](https://www.facebook.com/groups/emergin/permalink/1863754567195636/).

You can also use the LCD control. To preheat: `Prepare-> Preheat PLA (or Preheat ABS)`.  This method heats both the nozzle and the bed. You can also heat just the nozzle by `Control->Temperature->Nozzle`.

### Bowden tube maintenance
[Maintaining the Bowden tube](https://fbrc8.zendesk.com/hc/en-us/articles/205658894-Maintenance-How-Do-I-Maintain-My-Printer-): Over time, the Bowden tube can experience wear and tear, especially if you’re using more abrasive filaments. When you start to experience trouble feeding, it’s worth taking a look at your Bowden tube to check for any sign of damage. The feeder end of the Bowden tube should be slightly widened out to help facilitate feeding material. The print head end should be flat, and should be fully seated in the white PTFE coupler in the print head.

### Removing the Bowden tube

Push the coupler ring to maximum and pull the tube. But don't do that too many times, because [the tube material and coupler easily get damaged](https://www.facebook.com/groups/emergin/permalink/1863754567195636/).

# Bottom Plate Assembly

p22 The Bottom Plate assembly is relatively simple, simply follow the pictures on p22.  The Bottom Plate assembly might be simple, but the setting up and calibration of the heated bed is a cause for much frustration.  





Assembly:

- Before mounting the heated bed inspect the PCB side for visible damage.
- The two outer (thick) wires carries the large current to heat the bed. Polarity on these wires is not important.
- The heater resistance should be 1.5 to 1.7 Ohm.
- The two inner (thin) wires is connected to a thermistor embedded in the heat bed (where?) used to measure the bed temperature.  Polarity on these wires is not important.
- When not connected to the electronics the thermistor resistance should be 100 kOhm at 20 deg C.
- When connected to the electronics the thermistor resistance should be around 4.5 kOhm at 20 deg C.
- Optional: Rajaa Kahel chamfered the mounting holes in the build plate with a 6 mm drill bit to make the bolt heads flush with the surface of the bed.  This gives you the full size of the bed to print on. Just be careful with a hand drill on the wobbling bed, my chamfering attempts did not produce a neat result - perhaps use a drill press for this task.
- Set the height of the bed to approximately 13 mm.  Use a small object of the required size (someone used a Lego block) to help set the height.  The video shows the use of a vernier caliper; probably because it is easier to measure the offset, rather than to be minutely accurate.  The height of the hot bed will be finally adjusted later when bed levelling calibration is done, adjustment now does not have to be overly precise.
- The three bed screws have to go in quite deep, there is about 3-4 mm thread sticking out on the other side. This is convenient to add locking screws later.
- Fix the six  M6 tower mounting screws and nuts to the bottom plate, but don't tighten.

To set the bed at a height of 13 mm, the screw had to travel quite far - the spring is well compressed. Note the uneven chamfering attributable to poor control of my hand drill and the work piece.



The bed will not reach high temperatures when the cooling fans is blowing (reaching only 60-70 deg C max). With no forced air movement the bed should reach around 100 deg C. Someone mentioned that he speeds up the bed warm up by using a hot air  heat gun from the top.

Variations:

- Optional:  Add some noise damping feet (rubber, cork or similar) to prevent noise coupling to the table. Then also put the printer on a heavy and stiff base, such as granite.
- Optional: The build plate is suspended with three spring-loaded bolts.  The idea is that the springs pushes the build plate against the bolts.  [Rajaa Kahel](https://www.facebook.com/groups/emergin/permalink/1855806441323782/) does not like the fact that the build plate position is held in place with springs, so he used spacers with shims to adjust the build plate hard mounted to the frame, with no freedom to move.  The downside of this method is that there is no movement possible if the head crashes onto the bed.
- Some users complain that the screws loosen and the bed level is lost.   A set of double-locked nuts might help to prevent the screw nuts movement. Don't use Loctite.

<hr>

# Towers / Columns / Beams

All three towers are assembled the same. It does not seem that any one tower has preference over the other.



## Stuffing the tower empty space

I decided to put a piece of plastic conduit up each of the towers and then stuff  the tower with some plastic foam. I used some redundant laminate floor plastic under-mat foam sheeting, in a tightly rolled bundle about 15 cm long, jammed to about halfway down the tower (so the upper and lower portions were open).  I guess any firm material should suffice. if you can fill the full length of the tower it will be best.  Just stuff the material in there very very tight. Be careful not to cut your hands on the extrusion edges.

I am not sure what difference it will make to the noise levels, but at least I tried.  It does lower the ringing when the tower is struck with a metal object, so it should make some difference.



## Idler pulley p26

The idler pulley is meant to hold the one end of the belt in place.  The pulley should run free on the screw bolted to the tower. Lock the nuts on both sides of the extrusion. [Rajaa Kahel recommends](https://www.facebook.com/photo.php?fbid=701887786652707&set=p.701887786652707&type=3&theater) adding an additional M5 nut on the bolt that holds the idler pulley with less play, as shown in the third picture. The choice is up to you.

Assemble the pulley, but don't mount it in the tower just yet. It will be screwed in place just before fitting the belt.



## Tower stepper motor p24, p25

Before mounting any other component on the tower, first mount the stepper motor.  

In the Trium design the [NEMA-17](http://reprap.org/wiki/NEMA_17_Stepper_motor) stepper motors are hard mounted to the extrusion, inducing some noise into the frame.  E-Mergin [recommends](https://www.kickstarter.com/projects/873464596/trium-delta-3d-printer/posts/1763458) placing a damper between the motor and the extrusion (not part of the kit, buy separately) These are simply installed in between the tower extrusions and the motors with a total of 4 M screws (2 original one we are originally providing and 2 M3x4 for the motor side (3X each) ). The damper can be bought on [Ebay](http://www.ebay.com/itm/142210528617) or Aliexpress. Try to avoid the cork dampers, they appear to be [too thick](https://www.facebook.com/groups/emergin/permalink/1866102783627481/).



Mount the stepper motor with the connector to the outside/top of the tower to facilitate plugging in the cable.

So there are two options in mounting the stepper motor:

1.  Mounting without a damper: simply screw the stepper motor down with the four M3x14 screws provided, one in each corner.  In this mounting the motor spindle extends quite far beyond the extrusion.

2.  Mounting with the damper. In this mounting the motor spindle does not extend so far beyond the extrusion, but there seems sufficient exposed spindle length to mount the gear.  Follow this procedure to mount the motor:
  -  You may have to drill out some of the holes on the damper to full 3 mm bore, some seem to have M3 thread cut into the flange.
  -  Stick two M3 nuts to the damper with glue or double sided tape. Cut out the hole in the tape with a craft knife to allow the screw the pass through.  This serves to hold the nut in place for construction when screwing the motor to the tower extrusion. Sticking the nut to the damper is *not for permanent mounting*. It will become evident that it is almost impossible to mount the damper without this step: it holds the nut in place to screw into.
  -  Turn the damper upside down so that the two stuck screws are pointing towards the motor and place it on the motor.
  -  Using the other two holes (not those with the nuts), screw the damper firmly to the motor with two M3x4 screws (not in the kit, purchase this yourself).
  -  Position the motor (with damper) under the mounting holes in the extrusion, drop screws down into the nuts held by glue or double sided tape and tighten the screws. Do this carefully, otherwise you may loosen the nut.

3. Finally fit the GT2 gear on the motor spindle, but don't screw it down too tight yet.

This picture shows how the double-sided tape is used to hold the nuts in place on the damper.


## Slider assembly p24



When working on the sliders work careful with (1) the ball joints and (2) the plastic slider pieces.



Notes before you start building: 
- There is nothing holding the screw head in place. Once mounted in the tower you cannot get to this screw head.  It might be necessary to unscrew the nuts later (see later) which means that you cannot properly tighten the nut because you cannot get to the screw head. Of course, once glued in place you cannot remove the screw, but that is a small price to pay for the convenience of working on the slider in the tower. It should be possible to replace the slider plastic parts, but if it comes to the worst, you would have to buy a new slider assembly if the plastic parts wear out.  You decide it you want to epoxy or not.
- The tape in the slider issue: from the video and some postings it is seen that the slider must get a layer of tape on the metal carrier below the outer slider plastic. Perhaps the tape stuck to the slider is to take up some play between the slider and the tower. I added this layer of tape when I assembled the printer the first time, but found that the slide friction was higher than I expected. Later when printing I found that the stepper motor was missing steps (see below). When I disassembled the printer to add the epoxy to the slider screws, I decided to not put tape on again.  The slider resistance was much less without the tape, and there was no appreciable play on the slider. When you build, test the slider first before applying the tape. You decide yourself.

Do the following for each slider:

- Assemble the slider (one for each tower) as shown on p24.  There is no instruction on aligning the two parts, I did my best to eyeball the two parts well aligned. In other words the two parts are not obviously misaligned.  [digid](http://trium3d.proboards.com/thread/92/draft-version-building-guide#ixzz4XybuJ2SE)  proposed a method to set the slider alignment later after the slider is in place. It is for this procedure that you might decide to glue the slider screw heads in place.
- Look carefully at the nuts; there are two types of nuts in the kits: regular hex nuts and nylon insert nuts. Use the hex nuts first to hold the two parts together.  Later use the nylon insert nuts to fix the spring holder.
- Once two slider parts are mounted, carefully study the plastic slider: it consists of two parts.  The top part clicks off and separates from the carrier. Note that the top part is not symmetrical there is s ridge on the the long side, but only on one side. When you re-assemble just make sure that you put it back the right way, the other way won't fit.
- It you decide to epoxy the screw head: Mount and thoroughly tighten the both screws.  Unclip and remove the outer/upper plastic part, it comes away and exposes the metal part and the screw tops (see picture below).  Clean the cavity where the screw head is located with surgical spirits to remove all oils, and then placed a liberal drop of epoxy in the cavity, covering the screw head and filling all around the screw inside the cavity.  *Just be very careful that the epoxy don't leak through to below the screw head, or above the surface of the carrier.*  When the epoxy has partially hardened inspect the carrier to see if there is any epoxy on the surface of the carrier. Remove this excess epoxy (red arrows in the picture below) so that it does not interfere with the slider operation. The top surface of the cavity must be perfectly clean and flat.  Replace the plastic slider cover. Note in the picture below that I spilled some epoxy in the centre cavity (which will do no harm here) because the blob on the toothpick was too large and dropped before I reached the intended cavity.  I let the epoxy cure for two days before using the screw - it worked quite well, with the screw head held firmly in place while I tightened the nut.



- It you decide to add the tape:  Unclip and remove the outer/upper plastic part, it comes away and exposes the metal part and the screw tops. The type of tape [is apparently not important](https://www.facebook.com/groups/emergin/permalink/1868255326745560/) (I used 3M magic tape).  Stick the tape down and cut away the ends, to only remain on the flat surface of the carrier. Put back the slider plastic half to its original state.   You can now see the tape covering the screw tops through the holes in the plastic slider.  The picture below shows in blue where the epoxy must be applied (before covering with tape).



**Slider friction**
When building the printer I used tape in the slider assembly. When printing it appeared that the printer [might have lost steps](http://trium3d.proboards.com/thread/94/bed-positional-stability-good?page=1&scrollTo=799) on the X tower during calibration.  The [discussion on the forum](http://trium3d.proboards.com/thread/94/bed-positional-stability-good?page=1&scrollTo=799) pointed out a number of possible reasons: 
- A stiff slider, with friction too high for the stepper motor during fast movement.
- A stuck slider, where the slider was to large for the guide and had to be sanded to fit(!).
- The motor driver current was set to low.
- Feeding at too fast a rate (keep it below F3000 in the gcodes).

The following experiment was devised to try to quantify the friction. Despite the crude and inaccurate nature, it was still an interesting experiment because it demonstrated parity between the sliders.  First remove both belt ends from the slider, we want to measure the slider friction not the stepper motor inertia.  I used a cheap luggage scale to pull the slider up and observed the apparent weight - this can be translated to a force required to move the slider. The slider was moved for about 200 mm in one second.   The slides were always pulled up (the printer was turned upside down for the downward direction).  After correcting for the 160g mass of the scale itself, the scale indications (in kg) were as follows:

|-| X | Y | Z |
|-----|-----|-----|-----|
|Down | 0.59  | 0.36 | 0.32 |
|Up | 0.49|0.62| 0.44|
|Average| 0.54 |0.49  |0.38  |

It is evident that the sliders are within reasonable range of each other, none had grossly different friction from the other.  So this experiment indicated that there was no large differences here. I have no idea what the ideal value should be.



When I disassembled the printer to epoxy the slider screws I decided to not use tape again: the slider friction was smaller.
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

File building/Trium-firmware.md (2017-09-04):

# Trium Firmware

## Emergin RC7 Version
The standard Marlin open source firmware source is available [here](github.com/MarlinFirmware/Marlin) or one of the Release Candidate versions [here](http://marlinfw.org/meta/download/).  The E-Mergin web site provides a **modified** version of RC7, but note that the GitHub version has moved beyond RC7 (RC8 has *many* differences with RC7).  Be very careful to replace the TRIUM RC7 firmware with RC8 firmware. Ensure that you understand the differences between RC7 and RC8 as it pertains to the TRIUM.  E-Mergin provided the following [instruction](http://trium3d.proboards.com/thread/68/upgrade-marlin-1-rc8-planned) to upgrade from RC7 to RC8: download RC8, and replace the configuration.h and configuration_adv.h files using the the previous version files.

At least the following files are modified in the Trium hot end version of RC7 (relative to the Marlin standard RC7):
-  `_Bootscreen.h`: a new file not present in the standard Marlin distribution (possibly showing the Trium or E-Mergin logo?)
-  `Configuration.h`: a heavily modified file, for TRIUM printer info.
-  `Configuration_adv.h`: slightly modified for TRIUM printer info.
-  `Marlin.ino`: no significant changes, only TRIUMs weak attempt to time stamp.
-  `pins.h`: modified to only include the `pin_RAMPS.h` file, other file includes are removed
-  `pin_RAMPS.h`: slightly modified for TRIUM printer info.
-  `pins_xxxxx.h` a large number of pin definition files are removed, only `RAMPS.h` is retained.
-  `ultralcd.cpp`: slightly modified for TRIUM printer info.
-  `ultralcd.h`: slightly modified for TRIUM printer info.
-  `Version.h`: modified with TRIUM web site info.
-  `fonts/*.*` is a new folder containing some font info (possibly for the LCD).

The two TRIUM firmware versions (standard/DH and E3D) differ in the following file:
-  `Configuration.h`: different temperature sensor `TEMP_SENSOR_0`.
	-  The E3D uses sensor 5: "100K / 4.7k - ATC Semitec 104GT-2 (Used in ParCan & J-Head)"
	-  The standard hot end uses sensor 11: "100k / 4.7k beta 3950 1%".

## JohanV Marlin 1.1.5

[JohanV posted](http://trium3d.proboards.com/thread/144/marlin-1-5) a detailed description for preparing 1.1.5 for the standard Trium V1 with a single extruder.  He enabled thermal protection and adjusted the PID loop controller.

 Three files are affected: major changes to `Configuration.h`, minor changes to `Configuration_adv.h` and the entire `pins_RAMPS.h`.
And here they are: [Marlin115Trium3Dsingle.zip (43.86 KB)](http://trium3d.proboards.com/attachment/download/280).

Enable thermal protection (which hitherto was disabled) - you find this in lines 441 and 442 of `Configuration.h`:  

    #define THERMAL_PROTECTION_HOTENDS // Enable thermal protection for all extruders
    #define THERMAL_PROTECTION_BED // Enable thermal protection for the heated bed

1.  Download a  fresh [Marlin 1.1.5](https://github.com/MarlinFirmware/Marlin/archive/1.1.5.zip)  from github, and 
2.  Download [JohanV's zip file](http://trium3d.proboards.com/attachment/download/280)
3.  Copy the three files listed above from  [JohanV's zip file](http://trium3d.proboards.com/attachment/download/280) over the same files in the downloaded github folder.
4.  Make a note of the  Z probe offset by issuing the M851 command to your printer.
4. Compile and download to your Trium. 
6.  On Trium LCD  confirm that it reports Marlin 1.1.5 during start up.
7. Restore hard-coded defaults:    M502
8. Restore the Z probe offset M851 Z-1.7    //use the z probe offset for your printer.
9.  G33: Auto-calibrate 
10. M500:  to save the results, or you can hard-code the numbers that G33 came up with into 'Configuration.h' and then repeat the above, with the exception of the auto-calibration, of course.

JohanV [changed the following](http://trium3d.proboards.com/thread/144/marlin-1-5):

**Thermal Protection**   
If you use a damp cloth to clean hairspray from the heated bed, the newly-activated thermal protection declares a failure. To prevent these false alarms JohanV increased the time constant and allowable hysteresis on the bed (in `Configuration_adv.h`). If a thermistor should really fail the protection should activate. 

**PID Loop Calibration**  
Previously, the bed heating used bang-bang control.  JohanV activated the PID loop controller for the bed temperature control.  The bed (ID -1) PID optimisation  is similar to PID optimisation for the extruder.  
Marlin attempts to characterise the first extruder hardware (ID E0) by issuing 
M303 E0 S200 C8 telling it to heat, at full power until it hits 200 °C, and then letting it coast (for it overshoots significantly) until it falls back below the target temperature, and to repeat this for 8 cycles, observing its behaviour all the while. Then it calculates from these observations the Proportional, Integral and Derivative parameters for the control loop, which you can save using M500 (or copy back into `Configuration.h`, as was done here).

http://reprap.org/wiki/PID_Tuning  
https://www.youtube.com/watch?v=APzJfYAgFkQ  
https://forum.e3d-online.com/index.php?threads/pid-tuning.731/  
https://toms3d.org/2014/04/01/3d-printing-guides-using-marlins-pid-autotune/  
[https://oxi.ch](https://oxi.ch/2017/03/28/prusa-i3-and-all-marlin-based-3d-printers-pid-tuning-with-octoprint-slic3r-and-simplify3d/)  
https://en.wikipedia.org/wiki/PID_controller  

## More information

- [Configuring Marlin](http://marlinfw.org/docs/configuration/configuration.html)
- [How to flash](http://marlinfw.org/docs/basics/install.html)
- [Automatic Bed Levelling](http://marlinfw.org/docs/features/auto_bed_levelling.html)
- [Linear Advance extrusion algorithm](http://marlinfw.org/docs/features/lin_advance.html)
- [Marlin development](http://marlinfw.org/meta/development/)
- [List of GCodes understood by Marlin RC8](http://marlinfw.org/meta/gcode/)
- [Printer codes](http://trium3d.proboards.com/thread/7/printer-codes).

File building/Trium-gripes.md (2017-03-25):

# Introduction

The commercial world is a cruel and ruthless environment. There is little room for kindness and tolerance.  As a supplier, you are indeed aggressively working to take market share away from your competition; so can you really  expect kindness and tolerance?   In my open source endeavours I offer the fruits of my labour for free, and even there I find little kindness and tolerance. I agree that this situation is not commendable, but this is the way it is.  This is the world we live and compete in.

This document is not an attack on the E-Mergin company or team members. It is my evaluation of the Trium 1 printer as a commercial offering.  If your offering is not overall better than the competition, why should someone buy it?   Given the time I spent trying to get my Trium 1 printing, could have bought two built-up Original Josef Prusa i3 MK2 printers. They simply work.

I write this from considerable experience in aerospace engineering, software design and system engineering. I do not have prior 3D printing experience, but read extensively on the topic while waiting for the Trium.

# General notes

A prototype is not a product.  Many people can build prototypes. Few succeed in turning these prototypes into successful products.  A relatively small portion of the budget for new product development is spent on product design. Most of the resources are spent on documentation, quality assurance, produceability, debugging and improving reliability.  It appears that Trium 1 received mostly delta frame design attention with relatively little of remaining product development activities.  Trium 1 is not yet a smoothed out product - it should be regarded as a prototype basis for further experimentation.

The documentation is grossly incomplete and poor.  Exploded-view drawings are not assembly instructions.  I do not expect a 1000-page document, but some of the essential building topics are not  even mentioned.  There is not even a wiring diagram! Agreed, you do not have to tell the user how to develop a 3D STL model or how to operate Repetier, but at least give him some references to the many good books and resources on the internet. Unless a user has built hot-ends before, just throwing the parts at him with no instruction except an exploded view diagram is not acceptable.  Another example is the tape in the slider - shown briefly in the (poor) videos but no mention as to what, why or how.

Videos are no substitute for written documentation, but can be very useful additions to the written notes. But open your mouth and explain what you are doing and why it must be done.  Remember that the viewer must see, understand and internalise: the video should give sufficient time for this.  I found myself reversing and replaying most of the time, and even then not really understanding what I am supposed to do.

The performance of a delta printer depends critically on its mechanical integrity (alignment, mounting, firmware setup, etc) -- much more so than for a cartesian printer. Yet there is no mention of this, or even instructions on where to take special care.

Most of my issues are around maintenance and rework. Almost always, such work requires the disassembly of the printer, or at the very least turning it upside down.  The printer is definitely not maintenance friendly.

# Metal Frame

The Trium metal frame is indeed a beautiful work of art. It is very sturdy and has the potential to provide a stable printer mechanics.  The designers focussed so strongly on the stable metal frame that they lost perspective on the balance of the design. Compromises were made to other design considerations.

- The current design has high mechanical stability but not very good mechanical integrity. 
  - The extrusions slide into bent plates will ill-defined mechanical dimensions. Not all towers slide in to the same depth.
  - The endstop positions are left to change on PCB tolerance.  There is no mechanism to adjust the endstop position. Why is this important? The the endstop heights determines the z=0 plane. This plane must be perpendicular to all three towers. 

- Mechanical maintenance or rework is almost impossible, and almost always requires disassembly of the frame.  Once the top plate has been removed the mechanical integrity is lost.
  -  There is very limited access to the stepper motors once the Top Plate is in place. You have to take off the top plate to gain access or to change the stepper motors.
  - If you use a mechanical damper on the stepper motor, you have to disassemble the printer to get to the screws.
 -  There is severely limited access to the slider mechanics. Most screw heads are not accessible and requires removal of the Top Plate to take out the sliders for any rework or even tightening.
  - There is no instruction on how to align the slider such that the two balls are horizontal. It is surprisingly hard to align, and keep alingment, of this horizontal datum.

# Endstops and stepper motors

As described above, the endstops don't just stop the slider motion, the actually define the coordinate system.

- The endstop position is fixed by the holes in the extrusion and PCBs.  The position of the endstop depends on too many uncontrolled dimensions. There is no means to measure or adjust the height of the endstops.
- The alignment of the endstop switch levers and the slider mechanics is not very good.  The lever is touched on the side (about 10% overlap on my printer).  This led to unreliable contact and variation in the trigger height (up to 150 um on my printer). I had to print three parts to give the slider a wider, flat top surface for touching the endstop lever.
- The position of the three endstops determine the horizontal plane for the printer. If one switch is higher than the rest, the 'horizontal' plane is not perpendicular to the towers: the coordinate system is slanted.
- The presently used stepper motor is currently obtainable from one supplier only: jj-robotics in the UK. I spent many hours on the internet looking for this specific motor and it is only available from Motech (which does not sell in small quantities) and jj-robotics. I could not find it on Ebay, Aliexpress or Banggood.

# Rods and magnetic bearings

A cheap stainless steel (chrome plated?) ball was used.  Stainless steel has low magnetism and this required Emergin to add a spring to assist the magnetic hold force. 

The rod assembly was done by pushing the rod against the ball on one side while using some spacer on the opposite side. This means that rod at the shallow end scraped on the balls, leading to the rods scraping against the balls, thereby destroying the ball surface.  Some users found that after printing only three 1 kg filament rolls, it was necessary to replace the balls. 

I could not measure the rod lengths, but I suspect that the rods are not of equal length.  Unequal rod length can cause all sorts of problems because the delta kinematics depends critically on equality of rod length.

Many of the users I have contact with are moving to Haydn rods and balls as part of their remedial rebuilding. Why would I have to replace these parts after only a few months of operation? 

# Hot bed and z-probe

- The hot-bed height cannot be adjusted in real time with the nozzle moving around on the bed.  If the hot-end is near the screw, it covers the top of the adjustment screw, blocking access. The best you can do is to move the hot end away, do an adjustment and move the hot end back. This process is very time consuming: after you did this twenty times, it is not fun any more.
- The z-probe is a disaster. I received two different types (for my two hot ends), neither of which worked from the box.
- The z-probe is so far from the hot end that its utility is questionable.
- Even during the design phase it was evident that the z-probe was added in must because most modern printers offer it. It was a problem child in the design and was never really designed as an integral part of the system.  E-Mergin's subsequent statements that 'you don't really need it anyway' is just a cheap escape.
- The Marlin mesh bed auto-levelling simply did not work on my bed, the bed was too uneven.  When printing small object it was better to do manual levelling. I could not print large objects because of the poor quality of the bed.

# General layout

- Why do I have to turn the printer upside down (or at the very least lay it on its side) to gain access to the electronics in the Top Plate? Why can't the Top Plate be open at the top?
- Gravity is not working with us on the upside down electronics. Can we really rely on gravity to keep looms and connectors in place? Especially the low quality connectors used in the electronics?
- The fans

# Cheap electronics

- The quality of the mechanical frame is out of balance with the limitations of the supplied electronics  E-Mergin and many users scarcely built the printer but are now looking at new controllers, stepper drivers, printing beds, endstops, z-rpobes, etc.  Why is it necessary to replace the electronics on a newly designed printer? Emergin offered the lame argument that they had to keep the cost down. Granted, it makes sense - but then sell me only the frame and don't charge me for the lower performing electronics.

- The endstop mechanisms are suspect. In the Kickstarter offering E-Mergin offered a (theoretical) 10 micron accuracy. I fail to see how this is possible with the Trium 1 endstop design.  The promised 10 micron is clearly based on inadequate design calculations and without regard to build tolerance and hardware limitations.

- Too many users had to fix faulty electronics. If you buy from China, then at least have some form of quality assurance in your plant to ensure that the parts are working. I buy from an European commercial company with the expectation that the delivered parts will perform their intended function. Why buy from Europe if I can buy for cheaper from China?

# Quality Assurance

The metal parts probably had some form of outgoing inspection at the machine workshops.  The electronic parts were received from China and repacked for shipment.  There were many posts on the fora about inoperative boards, broken PCB tracks, short circuit PCB tracks, etc.

# Conclusion

I can add several more comments and remarks but all of the above are evidence of inadequate product design.  You simply do not put a product out in the user's hands if you have not built and tested at least a few printers in the intended user environment. Get a beta group to do your testing and fault finding for you, before you release to a wider audience.

The mere fact that there are a number of users replacing parts of their printers (EMergin developers were first to do this) with new and improved parts should tell you something of the design quality and maturity of the Trium 1.  Why do I have to pay the full price of a Trium 1 printer, but then replace most of the components to fix the design oversights?

So the lesson in this case study is: Make sure your prototype is a product before you ship large numbers.

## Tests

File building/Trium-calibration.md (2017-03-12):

# Conventions and assumptions

The notes below pertain to the following:

- The Trium delta printer (but should also apply to other delta printers).

- Marlin firmware RC7

- Repetier Host as a printer control software.

# Initial work

## Calibrating the bed levelling screws
If you have not yet installed the bed, measure the pitch on the bed screws. Count the number of thread ridges per measured distance. This gives you the pitch of the tread. If the pitch is known you can calculate the depth of travel for one turn. I counted 34 threads over a distance of 17.2 mm, which means 0.5059 mm pitch.  A quick search on the Internet revealed that the ISO standard coarse M3 thread pitch is 0.5 mm. At a pitch of 0.5 mm, this means as you turn the screw by a certain angle the bed moves 0.5 mm per revolution. The table below shows how much the screw will move during turning. 

| M3 screw turns | Bed displacement|
|---|---|
|1 turn | 0.5 mm |
|1/2 turn | 0.25 mm |
|1/4 turn | 0.125 mm |
|1/8 turn | 0.0625 mm |
|1/16 turn | 0.0313 mm |
|7.2 deg | 0.01 mm |

The movement in the table above would apply equally to the bed movement at the screw location. Suppose you are measuring the bed height radially at some fraction between the screw and the centre, and this measurement shows that the bed is 0.1 mm too high. The question now is: how much should the screw be turned to effect  required bed height change?

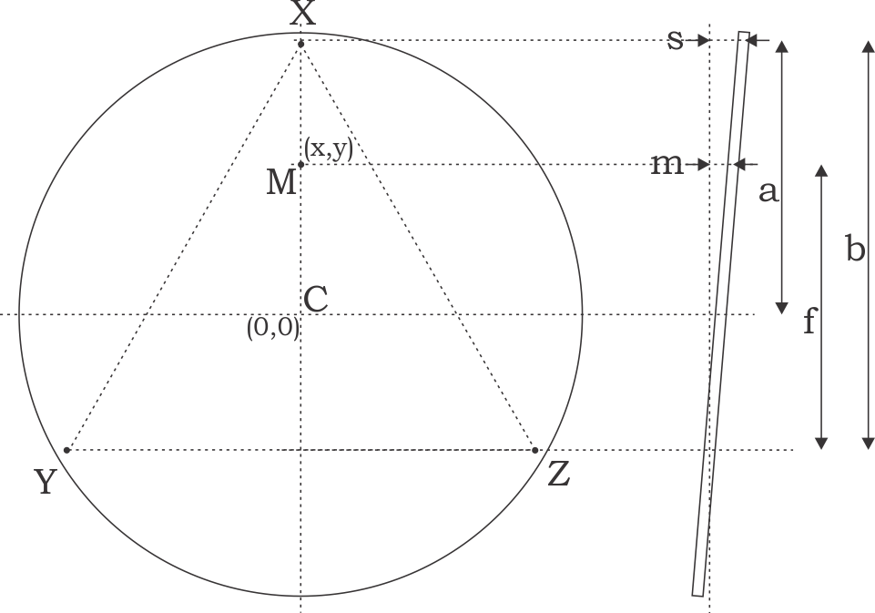
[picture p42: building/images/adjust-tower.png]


The screw is approximately 4.3 mm (3/8 inch) from the edge of the bed, so the screw radial distance to the centre will be  

a = 110-4.3 = 105.7 mm.  

If you turn the screw at the X tower, the bed movement is around the line drawn between the Y and Z towers. The distance from the screw to this line is  

b = a (1 + sin(30)) = 105.7 x 1.5 = 158.6

If the required vertical movement m at the measuring point is M, the screw vertical movement s will now be 

s = m * b / f

where f is the smallest distance between the measurement point and the YZ line. Using the (x,y) coordinates of the measurement point the screw movement becomes

s = m * 158.6 / (sqrt(x^2+y^2) +  52.85)

# Z-axis calibration p65

The top and bottom plates must be located on the three towers with no spaces between the towers ends and the top/bottom plates.  This is important because the frame integrity determines the coordinate system integrity.

Don't use the z-probe proximity bed levelling sensor in this procedure. The z-probe sensor will be adjusted and set up later.

- *Ensure that the printer nozzle is clean*, with no plastic below the nozzle level.  We want to calibrate the nozzle, not some gunk hanging below.  The picture below shows a small amount of filament protruding from the nozzle - this small amount is significant when it comes to z calibration (apologies for the poor quality picture, this is the best I could do with what I had).

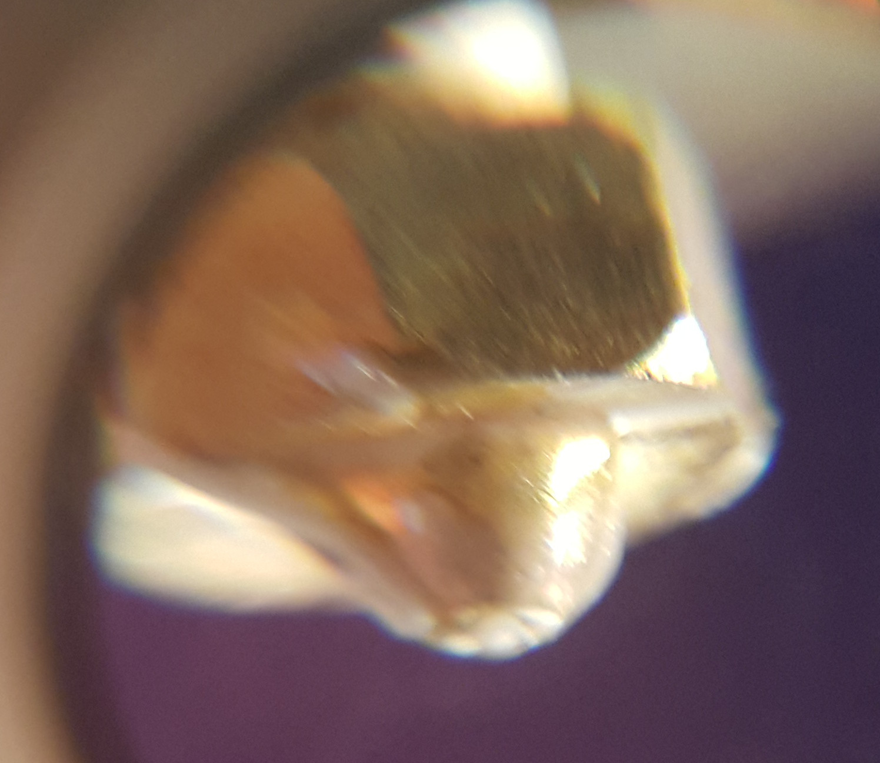
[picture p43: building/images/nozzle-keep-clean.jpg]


- Try to prepare the bed as you would print (hairspray, glue, PEI, or whatever), the bed preparation adds to the bed height.
- This procedure assumes that the Marlin firmware installed on the printer has  `MANUAL_Z_HOME_POS` set to 500.  Open the firmware and search in `configuration.h` for the line similar to `#define MANUAL_Z_HOME_POS 500`.  If the value is not exactly 500, change it to be 500.  This will enable the printer to go down by 500 mm from the home position. This means that the head will move beyond the bed, potentially damaging  the nozzle if the movement is too fast.  So, if and when you move down, be very careful.
- Place a sheet of clean unprinted paper on the bed (75 gms, 100 micron thick).
- Connect the printer to your computer using the USB port.
- Start Repetier on your computer. Go to `Printer Settings` and select the COM port you used to flash the firmware. Set the baud rate to 115200. `Apply` and `OK`
- Auto home: (1) use the LCD to go to `Prepare` menu and then select `Auto Home` or (2) give the `G28` gcode command with Repetier.  The printer does not remember the home position and it must be determined every time you switch on or reset/reboot  the printer.
- Manually take the head down to close to the bed. For a 440mm Trium use the gcode command `G0 Z100 F3000`  to get it down close quickly- but do not go any lower than around 100.   For a 220 mm Trium use the `G0 Z350 F3000` command.  To avoid loosing steps, don't use a feedrate higher than F3000.
- Manually jog down with ever smaller increments until the head just touches the paper.  There must be a very slight friction if you try to move the paper.

- Record the value on the display, say the value is xxxx.  In my printer and the regular head the value was 52.575.
- Open the firmware in the Arduino IDE, open the configuration.h file.  Search for 
		#define MANUAL_Z_HOME_POS
 (around line 812 in my file).  Change the entry to read 
        #define MANUAL_Z_HOME_POS (500-xxxx)
 in my case this was 
        #define MANUAL_Z_HOME_POS (500-52.575)
- Upload the new firmware.
- To test the new setting, repeat the above procedure from `Auto Home` and jog down.  The head should stop moving any further down on the paper and the display should show zero.

**Note:** once the value for `MANUAL_Z_HOME_POS` is set, the nozzle will never move below 0.  So even if commanded to go lower, it will stop at 0.

**Note:** at this point we have only set the Z_MIN value in the centre of the bed. If the bed is tilted, it may well happen that the nozzle can crash into a high area of the bed. So even with the value of Z_MIN set, be careful when moving the nozzle towards the bed.

[It seems then on the LCD control ](http://trium3d.proboards.com/thread/72/new-build-fired-today#ixzz4VuxgNRhq) you can move in 10 mm increments in X and Y but not in Z (no 10 mm movement in Z).  The LCD does provide 1mm and 0.1mm movement along the z-axis. Turning the LCD knob one position causes the head to move by 4 increments.  Rather do the 0.1 mm movements with  Repetier  instead.

The distance between the print bed and the nozzle is very important for print quality during the first layers. It seems that with the printer at Z_MIN the distance between the nozzle and bed must be around 0.1 mm.  See [here](https://ultimaker.com/en/community/16792-whats-the-best-distance-between-nozzle-and-bed-when-levelling), [here](https://ultimaker.com/en/community/5941-optimum-nozzle-bed-distance), and  [here](http://forums.reprap.org/read.php?1,582425).  I found it quite hard work to get the bed level and flat to within 0.1 mm.

See [here](https://www.facebook.com/groups/emergin/permalink/1861782507392842/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) for a long discussion on z calibration.

For another detailed description of the calibration process  [see here](http://reprapandme.blogspot.co.za/2014/02/first-tests-and-calibration.html).

# Z Probe

## Z probe firmware 

The firmware is set up to use three max endstops (the three switches) and one min endstop (the z-probe)

	//#define USE_XMIN_PLUG
	//#define USE_YMIN_PLUG
	#define USE_ZMIN_PLUG // a Z probe
	#define USE_XMAX_PLUG
	#define USE_YMAX_PLUG
	#define USE_ZMAX_PLUG
	#define Z_MIN_ENDSTOP_INVERTING false  // set to true to invert the logic of the endstop.

Depending on the logic of your endstop the value of `Z_MIN_ENDSTOP_INVERTING` must be set true or false. Note that `Z_MIN_PROBE_ENDSTOP_INVERTING` has no effect on the probe logic, it is not compiled into the Trium firmware.

For inductive sensors with an offset relative to the nozzle:

	#define FIX_MOUNTED_PROBE
	// Z Probe to nozzle (X,Y) offset, relative to (0, 0).
	// X and Y offsets must be integers.
	//
	// In the following example the X and Y offsets are both positive:
	// #define X_PROBE_OFFSET_FROM_EXTRUDER 10
	// #define Y_PROBE_OFFSET_FROM_EXTRUDER 10
	//
	//    +-- BACK ---+
	//    |           |
	//  L |    (+) P  | R <-- probe (20,20)
	//  E |           | I
	//  F | (-) N (+) | G <-- nozzle (10,10)
	//  T |           | H
	//    |    (-)    | T
	//    |           |
	//    O-- FRONT --+
	//  (0,0)
	#define X_PROBE_OFFSET_FROM_EXTRUDER -33.5     // X offset: -left  +right  [of the nozzle]
	#define Y_PROBE_OFFSET_FROM_EXTRUDER -5   // Y offset: -front +behind [the nozzle]
	#define Z_PROBE_OFFSET_FROM_EXTRUDER 0  // Z offset: -below +above  [the nozzle]

The (x,y) offsets is known from the design: how far is the probe centre displaced from the nozzle in x and y. The standard Trium design is (-33.5,-5).  Initially, however, the z probe z offset is not known. The sensor is mounted with some tolerance in the z direction, hence the z-height is not normally fixed by design (see below for z-probe calibration).

The z probe is connected to the zmin endstop inputs on RAMPS:

	#define Z_MIN_PROBE_USES_Z_MIN_ENDSTOP_PIN

The changes in z height used when deploying, stowing, and using the z probe are set here:

	#define Z_PROBE_DEPLOY_HEIGHT 15 // Raise to make room for the probe to deploy / stow
	#define Z_PROBE_TRAVEL_HEIGHT 5  // Raise between probing points.

You can adjust the vertical (z) offset between the nozzle and the z probe (see M851 below).  The allowable limits for the z probe vertical offset is defined in the firmware here:

	#define Z_PROBE_OFFSET_RANGE_MIN -20
	#define Z_PROBE_OFFSET_RANGE_MAX 20

The g30 work is done in the function `run_z_probe()` in `Marlin_main.cpp`. The essential contents are:
- At the current (x,y) position move fast to `home_bump_mm(Z_AXIS)`, which appears to be z=5. Speed is `Z_PROBE_SPEED_FAST` is (50*60)=3000.
- Move slowly from the current position by twice `home_bump_mm(Z_AXIS)`, i.e., to z=-5. Speed is `Z_PROBE_SPEED_SLOW` which is `Z_PROBE_SPEED_FAST`/2 is (50*60/2)=1500.
- Clear the z endstop bits to suppress a report.
- When the z probe triggers (sensed as a z endstop hit), stop movement, get the current z axis position, process and then return the value as z height.

It appears that `run_z_probe()` resets the bed levelling parameters (at least temporarily when doing g30).

## Calibrating the z probe offset

First check that the probe works. Send it an [M119 gcode](reprap.org/wiki/G-code#M119:_Get_Endstop_Status): Returns the current state of the configured X, Y, Z endstops. Takes into account any 'inverted endstop' settings, so one can confirm that the machine is interpreting the endstops correctly.  So send M119 and see that z probe shows a “L” for low = not triggered. Now trigger it by hand while sending M119 again. Now probe value should show a “H” for high = triggered. If it is the other way around you need to change `Z_MIN_PROBE_ENDSTOP_INVERTING`. If nothing changes you need to fix the hardware problem (wiring, power supply, etc.).

The procedure below assumes that the probe is mounted higher than the nozzle, i.e., the nozzle will hit the bed before the probe does.

Ensure that the nozzle is clean with no plastic sticking out the bottom. We want to measure the height of the nozzle metal tip.

The inductive probe trigger distances to different types of metal are different, so be sure to do all measurements relative to the bed itself.

You may want to preheat the bed and nozzle to the print temperature before doing levelling.  

The procedure is as follows:
- Move the probe to (0,0,5). The probe is offset relative to the nozzle, so give gcode command (where the x and y values are meant to move the probe (x,y) to (0,0,X)):

		G28
		G0  X33.5 Y5 Z5 F3000  ; move probe to (0,0,5)

- Observe that the nozzle is offset from the centre of the bed, and that the probe is directly above the centre of the bed.

- Send a [G30](http://reprap.org/wiki/G-code#G30:_Single_Z-Probe) command to the printer to do an auto probe and note the z value returned in the log screen, it should be something like the following. Ignore the time x and y values, only make a note of the z value. This is the hotend z position at which the probe triggers (in this case 0.69 mm above the bed).  Note that this is not the trigger distance to the metal surface.

		20:59:21.321 : Bed X: 0.00 Y: 0.00 Z: 0.69

- After the G30 command the probe  should be in the same (x,y) position but 15 mm above the bed.  If you wish you can now repeat the same process manually by moving the hotend down using the jogger in Repetier. Initially move with large increments, but then with smaller increments as  you approach the z value given by G30.  The value should be much the same as was obtained by G30. So this step is optional, but there is a certain satisfaction when doing the manual probing.

- Move the *nozzle* to (0,0,5). Execute a home command first to make sure that we work from a calibrated position.

		G28
		G0  X0 Y0 Z5 F3000 ; move nozzle to (0,0,5)

- While moving a piece of unprinted paper or a shim of known thickness (say 0.1 mm) between the nozzle and the bed, drop the nozzle down using Repetier's jogger, slowly towards the bed. Start with large increments but as you approach the bed, use smaller increments, down to 0.01 mm.  Make a note of the z value where the paper experiences some friction.   Suppose the z value where the friction point occurred is at 0.15 (with the paper/shim in place).

- Now do the calculation. Denote the probe trigger height as zprobe, the nozzle friction height as znozzlemeasure, the shim/paper/feeler gauge thickness as zshim,  and any hairspray tape or other non-metal layer thickness as zcoat.  The nozzle-to-probe-trigger offset is given as shown in the following figure.  Note that the actual bed height (zbed), coating thickness (zcoat), and trigger distance (ztrigger) do not affect the calculation; the relative nature of this procedure automatically accounts for these values. The only absolute measurement required is that of the shim thickness (zshim).    
In our example the nozzle-to-probe offset is 0.69-0.15+0.1=0.64 mm.

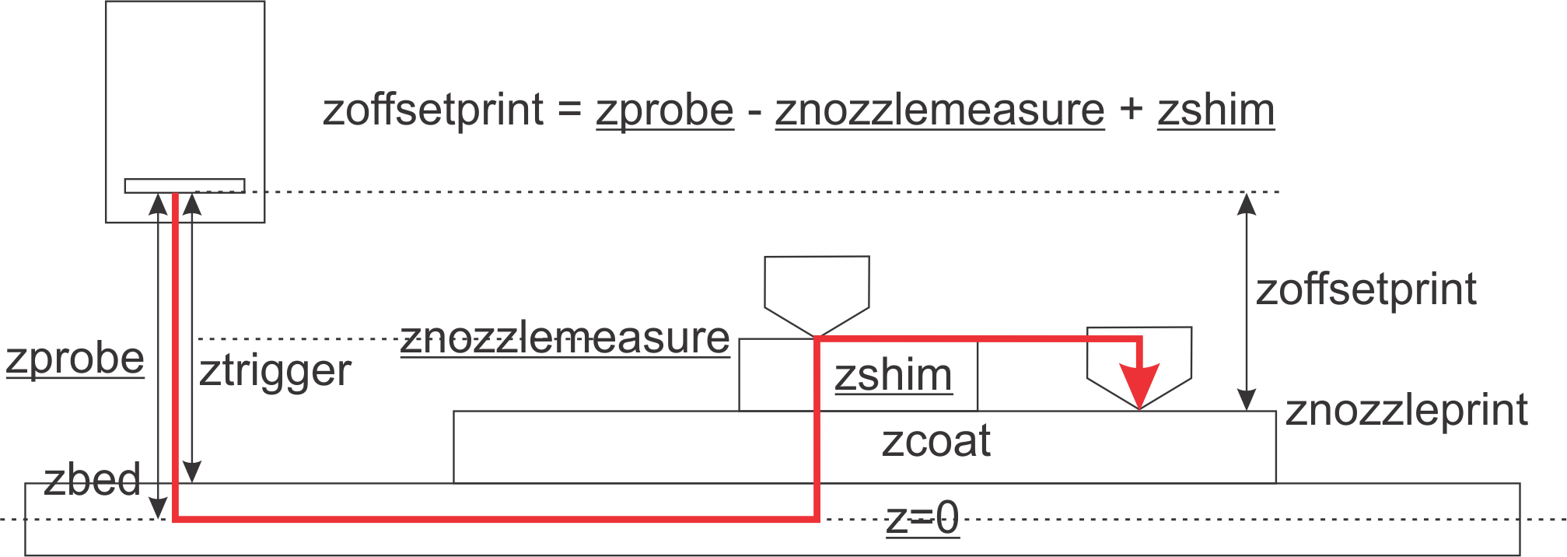
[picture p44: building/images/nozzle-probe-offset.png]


-  Set the offset value by using the [M851](http://reprap.org/wiki/G-code#M851:_Set_Z-Probe_Offset): Sets the Z-probe Z offset. This offset is used to determine the actual Z position of the nozzle when using a probe to home Z with G28. This value may also be used by G29 to apply correction to the Z position.  This value represents the distance from nozzle to the bed surface at the point where the probe is triggered. This value will be negative for typical switch probes and inductive probes. After setting the limits with M851.

		M851 Z-0.64 ; set probe 0.64 mm higher than the nozzle 
	
- Display the offset by using M851 without parameters:

		M851

- Store all current settings permanently with [M500](http://reprap.org/wiki/G-code#M500:_Store_parameters_in_EEPROM) to EEPROM.

		M500        ; store value in EEPROM

# Manual bed levelling: adjusting the screws

The material in this section is a variant of the procedure described [here](http://minow.blogspot.co.za/index.html#4918805519571907051).

A sheet of paper is used as a feeler gauge: lower the nozzle to the point where the paper has some friction when moved under the nozzle.  If the paper is not able to move, the nozzle is too far down and you are in fact pushing the bed down.  If the paper moves freely it means that the nozzle is not yet in the desired location.

By the way, you can calibrate the thickness of your printing paper by taking 10 sheets and then measuring the thickness with a vernier caliper.  Measure the thickness in several different locations, take the average and then divide by 10.

Program the following Repetier buttons (if the bed is well manually levelled, you might set the z value to 2):

|Button 1| Position |Command |
|----|----|----|
|1 | Centre | `g0 z52 x0 y0 f3000`|
|2 | X tower| `g0 z5 x-82.2724  y-47.5 f3000`|
|3 | Y tower| `g0 z5 x 82.2724  y-47.5 f3000`|
|4 | Z tower| `g0 z5 x0 y95 f3000`|

Button 1 moves the nozzle to the centre.
Buttons 2 to 3 move the nozzle towards the X, Y, and Z towers at a radius of  95 mm from the centre.  I don't want to go too close to the bed screw, in case there is a distortion in the plate at the screw position.  The three tower calibration positions on my printer are shown here (about 15 mm from the edge):

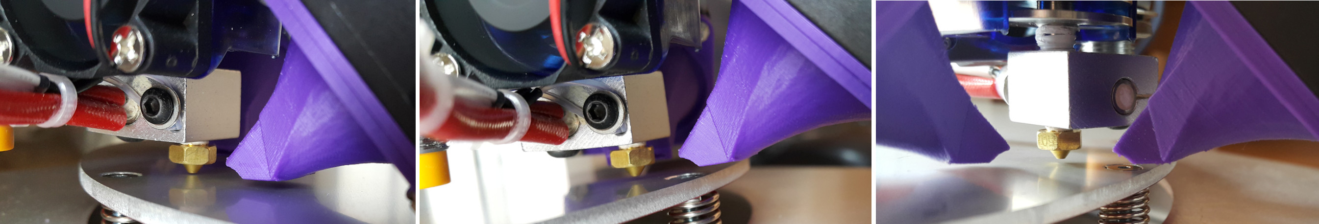
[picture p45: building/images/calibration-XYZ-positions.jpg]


In the previous section we set the value for Z_MIN in the centre of the bed.  At present the bed may still be in a  tilted orientation.  This procedure attempts to adjust the bed heights at the bed mounting screws (aligned with the towers).  The idea is to measure the height of the bed near each of the screws and then adjust the height of that screw. The procedure is as follows:

- After installation level the bed manually with a measuring block or a vernier caliper so that the bed is level, relative to the fame, to within 0.5 mm. Measure by hand and adjust till the bed is at the same height at all three screw positions. This step is really important, because it makes the next steps easier and faster.
- [MiR advises](http://trium3d.proboards.com/thread/94/bed-positional-stability-good?page=1#ixzz4YBplrXpU) to  take an Allen wrench that is exactly 10mm high and adjust the screws of the bed so that the wrench barely slides through the gap between the bed and the chassis. This is an easy way to make sure that the bed is properly levelled.
- Using the procedure described above for z-calibration, measure the height of the bed at all four positions. This is most easily done using Repetier and the four button scripts. If any of the four positions is at a height of 0 mm it means that the bed could be lower, the firmware just stopped at 0 mm.  In this case change the Z calibration calculated in the previous section. Set the value of xxx to be 0.5 mm smaller, so that the nozzle can move further down (just remember that this could be lower than the bed, so the nozzle or bed can be damaged if you move to z=0).  Repeat the procedure until none of the four readings is zero, every time increasing the value by 0.5 mm.
- Move the nozzle to the X-tower screw (Button 2 `g0 z5 x-82.2724  y-47.5 f3000`), with the nozzle say 5 mm above the expected build plate. 
- Carefully lower the nozzle initially at 0.1 mm and later at 0.01 mm at a time until the nozzle distance is a paper thickness from the plate. When you move a single sheet of paper between the bed and the nozzle it should experience some friction, but not too much (because you are then compressing the paper).
- Take note of the z value. If the z value is zero it means that the bed edge is probably below the centre (remember that the nozzle cannot move below zero), then set the bed level slightly higher (see two steps back).
- By the way, I found that there is considerable hysteresis (0.05 to 0.15mm) between (1) moving the nozzle down to touching the paper and (2) moving the nozzle  up to releasing the paper.  In most fine mechanical systems this is unacceptably large. In the delta printing mechanism this hysteresis is probably acceptable, provided we always only move in one direction (i.e., avoiding the the hysteresis gap).  So when you do bed levelling always test while moving down. If you moved too far down, go up again by 0.5 mm before dropping the nozzle down again.  When printing the nozzle is always moving up, if it was to go down, it will destroy the print or bed.
- Repeat the procedure for the Centre (button 1),  the Y (button 3) and the Z (button 4) tower positions. Each time taking a note of the z value where the nozzle is paper thickness above the bed.
- Review the three values at X, Y and Z and the centre of the bed then decide at which level you want to set the bed edges.  But all the time make sure that you don't get a false z=0 reading (the nozzle cannot go lower than 0).
	- If the centre is lower than the lowest edge, aim to set the bed edges higher than the centre. In other words use the Z_MIN value at the centre as reference and adjust the edges to be higher. 
	- If the centre is higher than the highest edge, set all the edge heights to be equal but lower than the centre.
-  Repeat the process, iteratively measuring the values at C, X, Y and Z.   Adjust the bed level at each of the towers to get the same value at all three towers. 
- Move the nozzle to home (to calibrate the top endstops)  and repeat the measurements, until the values at the bed edges settle to the same value.
-  After about three or four iterations around the circle, my bed printer's bed levels settled down on

|C |X |Y|Z|
|----|----|----|----|
|0.72|	1.26|	1.26	|1.26|

The bed is now level (edges at the same height), but it is clear that the centre measures a displacement of 0.55 mm lower than the edges.

Note that the print area is not a 200 mm diameter circle, but a [Reuleaux triangle](https://en.m.wikipedia.org/wiki/Reuleaux_triangle).
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

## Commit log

2017-02-21 Moved some material to new documents.
2017-03-05 Added description for automated bed measurement and manual levelling.
2017-03-06 more work on z-probe for manual bed levelling
2017-03-09 Major rework in calibration file, moved info in a more logical flow.
2017-03-10 completed section on zprobe offset calibration
2017-03-12 added gcodes and Jupyter notebook for full bed probing
2017-03-13 added 84 sample file
2017-03-13 more info on bed flatness measurement
2017-03-15 added best fit bed correction
2017-03-15 added more info on bed unevenness
2017-03-18 added slider hat
    [TriumSliderHat.scad, TriumSliderHat.stl]
2017-03-19 more work on bed sanding to level
2017-03-21 added rod scraping picture
2017-03-22 reduced the number of samples at extremes
2017-03-22 added two pictures of the corrected bed
2017-03-23 added picture of the printer
2017-09-04 starting on marlin firmware docs
